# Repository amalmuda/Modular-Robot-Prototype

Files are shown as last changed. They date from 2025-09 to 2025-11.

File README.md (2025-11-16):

# The MATS - Modular Actuated Transforming System

MATS (Modular Actuated Transforming System) is a modular robot with two types of modules: Brick modules for connections and Joint modules with actuated servos. Unlike many modular robots, MATS allows easier morphology changes without manual disassembly and reassembly for each configuration.

The cable management of robotic systems like this can often also become messy, with wires running between modules. This project focused on creating a clean, efficient system with screw-free, robust connections to simplify assembly and maintain functionality. A unique feature of this robot is the absence of core modules; all Brick modules are identical, simplifying assembly and ensuring consistent functionality. I focused on a minimalist yet functional design to simplify manufacturing while ensuring intuitive use and visual appeal, covering both the fastening mechanism and cable management.

The modules are inspired by Revolve2, which is a framework focusing on modular robotics. The software used
to directly control the robot is the Dynamixel SDK, a software development kit that supports multiple programming tools and languages, including Python and ROS. For this project, I programmed the robot’s movements using Python and tested various custom movements that I developed. The robot communicates directly with a PC via a U2D2 USB communication converter.

This project developed a durable, visually appealing modular robot with easy-to-assemble modules, seamless connections, and efficient cable management. Its minimalist design simplifies use and supports future advancements in modular robotics.

## MATS Demo Video (dancing mode)

<p align="center">
  <a href="https://www.youtube.com/watch?v=7X1GoiLjF7E">
    MATS demo video (dancing mode)
  </a>
</p>

<p align="center">
  <b> Click the image to watch the MATS demo on YouTube (with sound)</b>
</p>

## Modular robot crawling

<p align="center">
  <a href="https://www.youtube.com/watch?v=GOCKxC3IZR8">
    Modular robot crawling
  </a>
</p>

<p align="center">
  <b>Click the image to watch on YouTube</b>
</p>

## Other configuration examples

<table>
  <tr>
    <td align="center">
      <a href="https://www.youtube.com/watch?v=6TiiAdvZFsY">
        Small worm configuration
      </a><br>
      <b>Small worm configuration</b><br>
      <sub></sub>
    </td>
    <td align="center">
      <a href="https://www.youtube.com/watch?v=PtgOzKhWjz0">
        Riverdancing quadruped
      </a><br>
      <b>Riverdancing quadruped</b><br>
      <sub></sub>
    </td>
  </tr>
  <tr>
    <td align="center">
      <a href="https://www.youtube.com/watch?v=ytFvpS4uCtc">
        4-legged breakdancing spider
      </a><br>
      <b>4-legged breakdancing spider</b><br>
      <sub></sub>
    </td>
    <td align="center">
      <a href="https://www.youtube.com/watch?v=Mg6dMusM-d4">
        Large snake configuration
      </a><br>
      <b>Large snake configuration</b><br>
      <sub></sub>
    </td>
  </tr>
</table>

# Tools and bill of materials

The following components were used in the development of MATS:

- U2D2 USB communication converter
- U2D2 Power Hub Board
- Dynamixel AX-18A servo
- 3D printed modules with PLA and ABS (CAD modelled in SolidWorks)
- Neodym magnets

**Complete list of bill of materials:**

Main components:
| Item | Description | Quantity 
| ---- | --- | ---
| 1 | Robotis U2D2 USB communication converter | 1 
| 2 | Robotis U2D2 Power Hub Board | 1 
| 3 | Dynamixel AX-18A servo | 8

Mounting components:
| Item | Description | Quantity 
| ---- | --- | ---
| 1 | Dynamixel-AX Bioloid FP04-F2 frame | 8 
| 2 | Dynamixel-AX Bioloid FP04-F3 frame | 8 
| 3 | RS PRO Neodym magnet 2.09 kg - 12 mm | 52

Connectors and wiring:
| Item | Description | Quantity 
| ---- | --- | ---
| 1 | Robotis 3P Extension PCB | 9 
| 2 | 3P Molex male to female adapter| 36 
| 3 | Self-assembled 3P Molex cable 4 cm | 36 
| 4 | Self-assembled 3P Molex cable 8 cm | 16 
| 5 | Self-assembled 3P Molex cable 18 cm | 16
| 6 | Self-assembled 3P Molex cable 50 - 100 cm | 1  
| 7 | Micro USB cable | 1  

Fasteners:
| Item | Description | Quantity 
| ---- | --- | ---
| 1 | Bioloid Plastic Busher BPF-BU| 8 
| 2 | Bioloid Plastic Washer BPF-WA| 8
| 3 | M3 bolts| 8
| 4 | M2 screws | 164
| 5 | M2 nuts | 32  

For 3D-printing:

| Part  | Material | Quantity | Infill | Layer height
| ----- | --- | --- | --- | ---
| Block module | ABS | 9  | 20 % | 0.2 mm 
| Servo holder | ABS | 16  | 20 % | 0.2 mm 
| Lid | PolyMaker PLA | 18  | 20 % | 0.2 mm 
| Power Hub Board base | PolyMaker PLA | 1  | 20 % | 0.2 mm 

## Firmware/software for the robot/prototype

Set up the environment:
```
$ conda create --name mats_env --file requirements.txt
$ conda activate mats_env
```
After installation, make sure:
- U2D2 Power Hub Board is turned ON and connected to the robot
- USB from the U2D2 is connected to your computer to the right port

Then you can run your Python files from the src folder with examples:
```
python breakdance.py
python wake_up.py
python dance.py
```
## Future work

### Design

- **Integrate Molex connectors:** Combine with mating connectors for seamless integration and use magnets for attachment and servo communication.
- **Expand connectivity:** Modify Brick modules for six-sided connectivity instead of four-sided to increase flexibility.
- **Add adapters:** Develop connectors for linking modules directly, including 360° revolute joints for modular manipulators.

### Hardware and software

- **Use a microcontroller or a Raspberry Pi:** Enable wireless control and communication with the robot.
- **Incorporate a battery as the power source:** Address the challenge of module size, or consider a core module to house the battery and hardware.
- **Use simulations, evolutionary algorithms, and artificial intelligence:** Optimize the robot’s movements efficiently.
- **Address the reality gap:** Develop methods to transfer optimized movements from simulations to the real-world robot, minimizing performance differences.

## Image gallery

<table>
  <!-- Row 1: evolution spans two columns -->
  <tr>
    <td align="center" colspan="2">
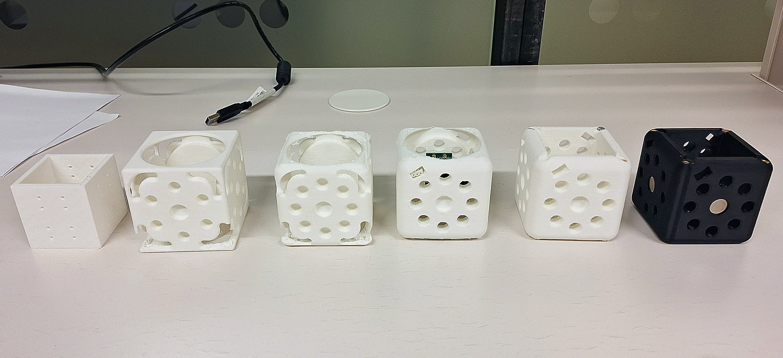
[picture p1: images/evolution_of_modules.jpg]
Evolution of the module design
      <br>
      <sub>Evolution of the module design</sub>
    </td>
  </tr>

  <!-- Row 2: assembled + exploded views -->
  <tr>
    <td align="center">
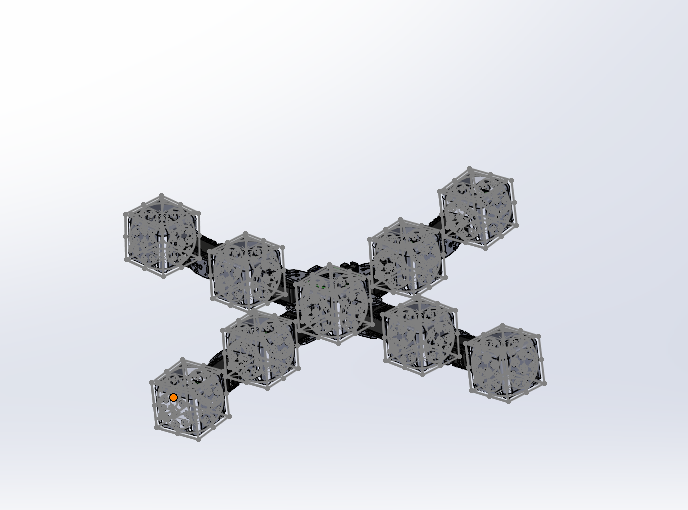
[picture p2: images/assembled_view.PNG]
Assembled module view in SolidWorks
      <br>
      <sub>Assembled module view in SolidWorks</sub>
    </td>
    <td align="center">
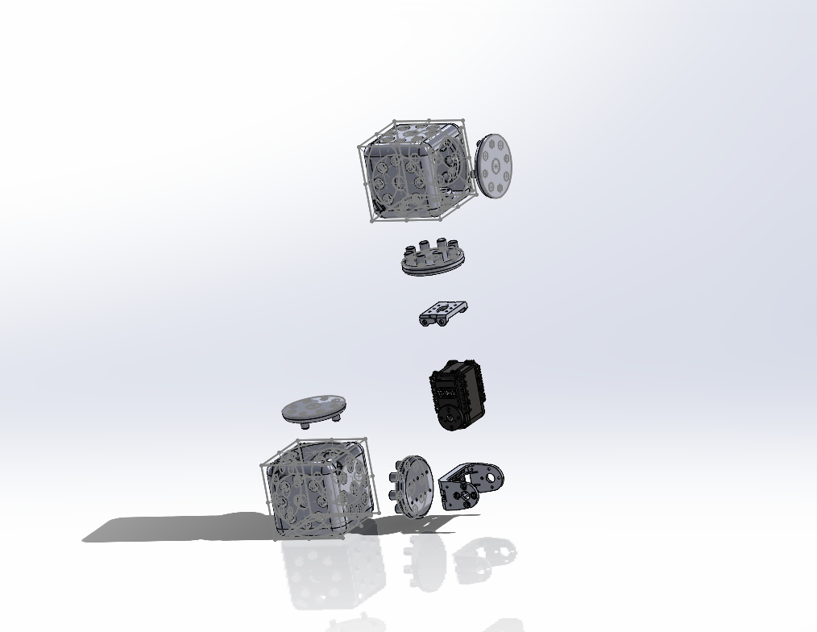
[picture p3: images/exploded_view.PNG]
Exploded module view in SolidWorks
      <br>
      <sub>Exploded module view in SolidWorks</sub>
    </td>
  </tr>

  <!-- Row 3: latest module + power hub -->
  <tr>
    <td align="center">
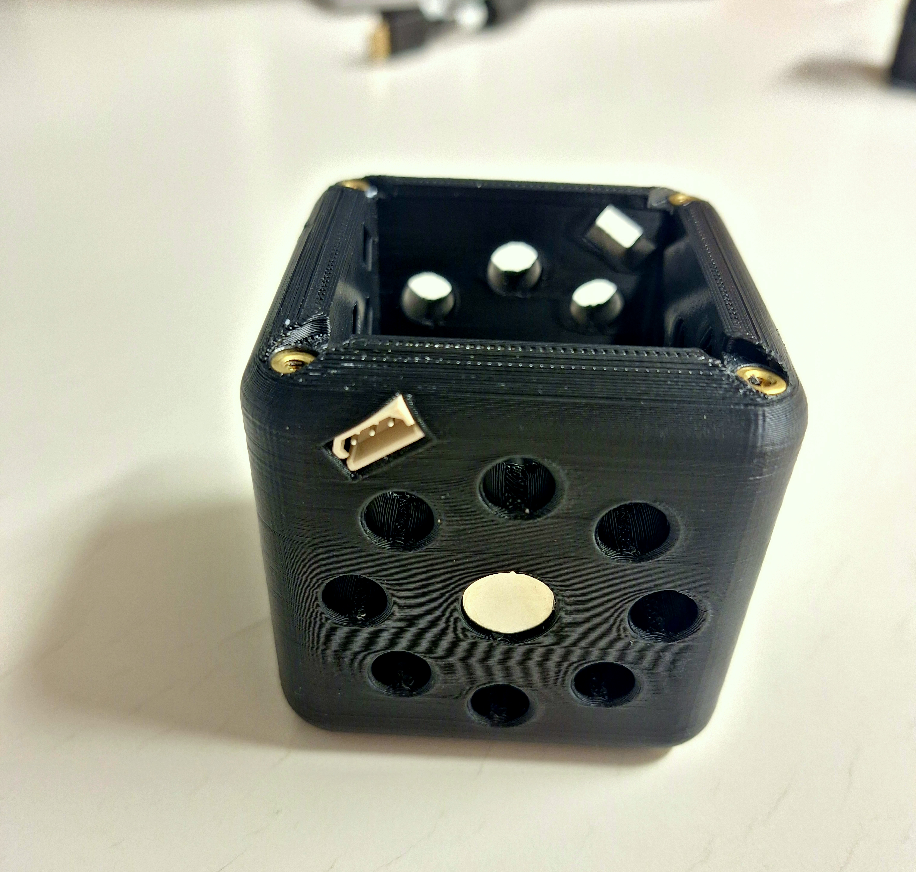
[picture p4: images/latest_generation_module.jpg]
Latest-generation module (ABS)
      <br>
      <sub>Latest-generation module (ABS)</sub>
    </td>
    <td align="center">
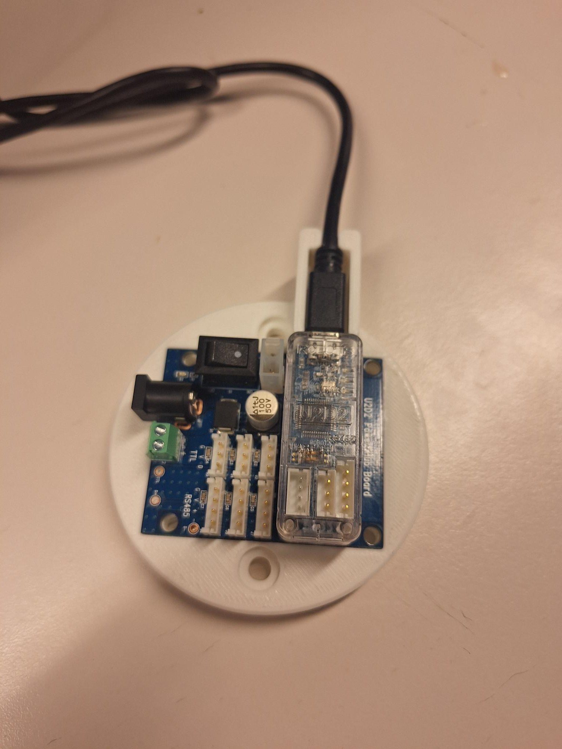
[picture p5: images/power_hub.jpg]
Power hub and control electronics
      <br>
      <sub>Power hub and control electronics</sub>
    </td>
  </tr>

  <!-- Row 4: spider simulation + robot in action -->
  <tr>
    <td align="center">
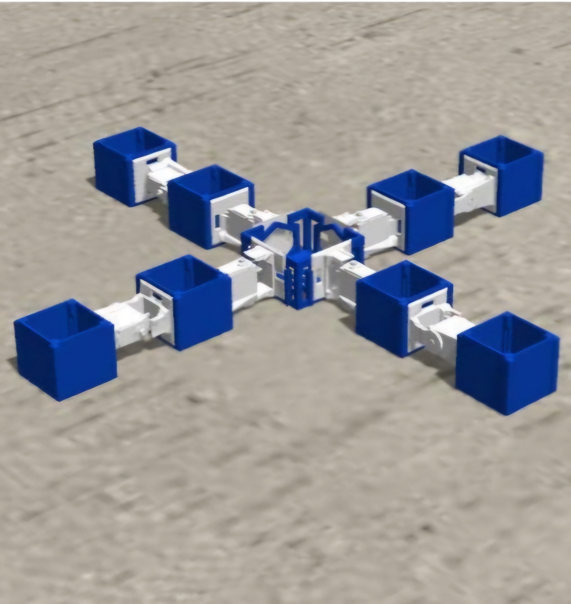
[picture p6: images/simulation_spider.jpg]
Spider-robot simulation in Revolve
      <br>
      <sub>Spider-robot simulation in Revolve</sub>
    </td>
    <td align="center">
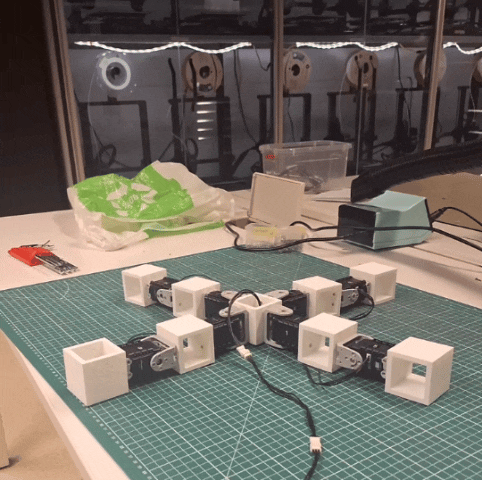
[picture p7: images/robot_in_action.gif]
Robot in action
      <br>
      <sub>Robot in action</sub>
    </td>
  </tr>
</table>

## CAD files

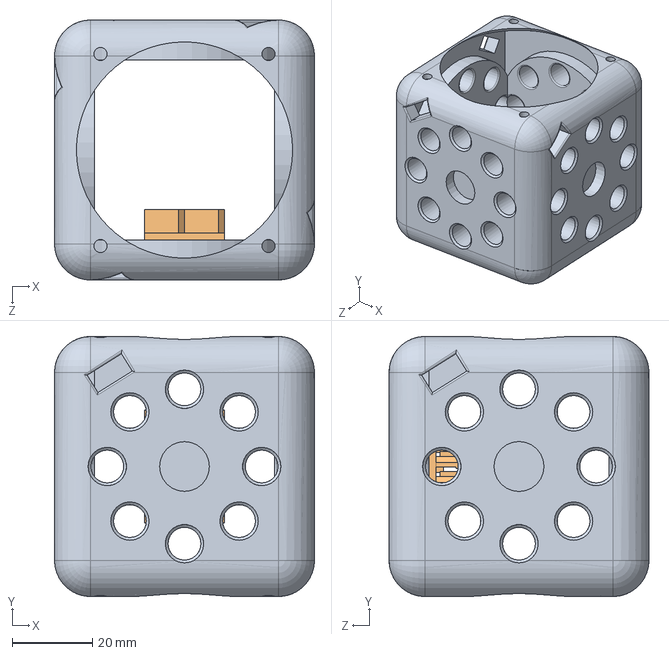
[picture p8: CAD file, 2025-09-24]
solidworks/brick_module_with_component.SLDASM
65.0 x 65.0 x 65.0 mm
brick_module
3P Extension PCB

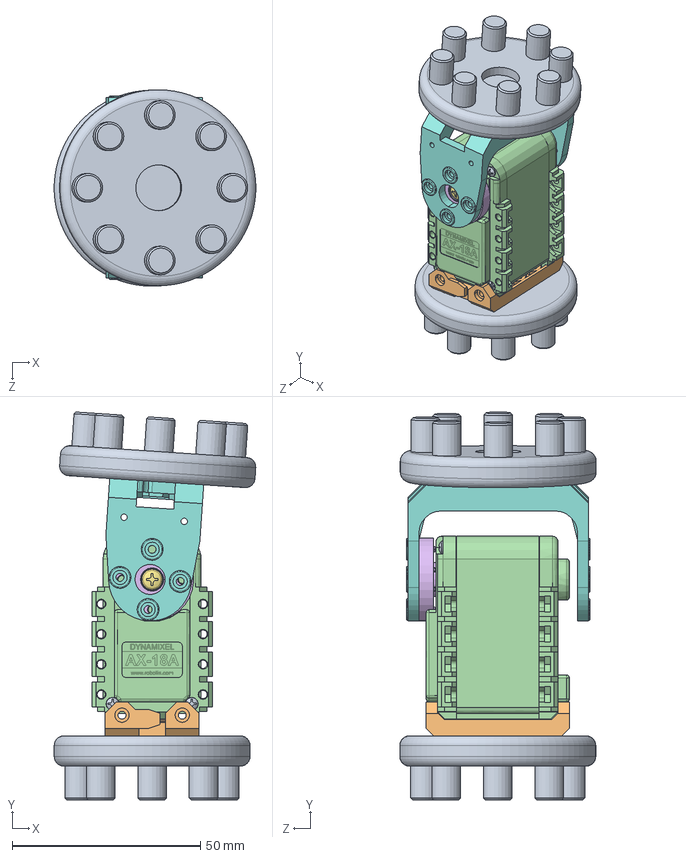
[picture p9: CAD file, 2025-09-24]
solidworks/servo_module.SLDASM
53.5 x 102.9 x 52.1 mm
Cover Screws^joint x 4
Insert M3^joint
3 Pins Connector^joint x 2
Body^joint
Wheel Gear^Horn Assembly_joint
Horn^Horn Assembly_joint
BHS M2x8^Horn Assembly_joint
FP04-F2.stp
servo_module x 2
FP04-F3.stp

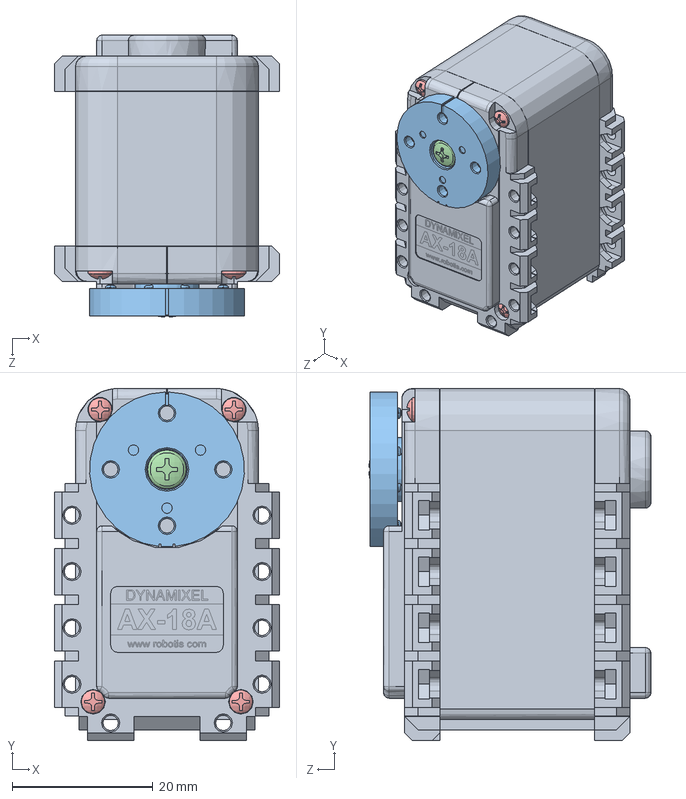
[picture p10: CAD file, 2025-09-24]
solidworks/Dynamixel AX-18A.SLDASM
32.0 x 50.0 x 40.1 mm
Body^AX-18A
Wheel Gear^Horn Assembly_AX-18A
Horn^Horn Assembly_AX-18A
BHS M2x8^Horn Assembly_AX-18A
Cover Screws^AX-18A x 4
3 Pins Connector^AX-18A x 2
Insert M3^AX-18A

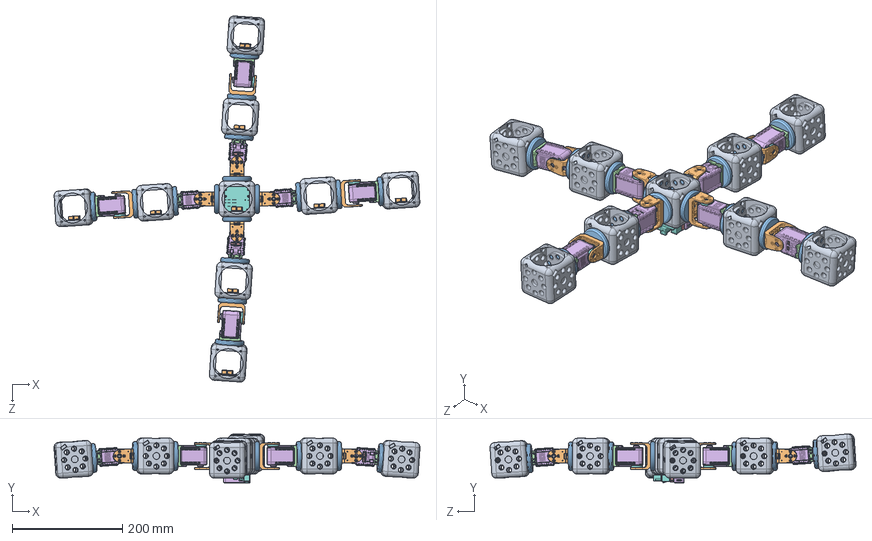
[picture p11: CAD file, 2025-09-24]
solidworks/assembled_spider_robot.SLDASM
663.6 x 88.8 x 663.5 mm
brick_module x 9
3P Extension PCB x 9
Cover Screws^joint x 32
Insert M3^joint x 8
3 Pins Connector^joint x 16
Body^joint x 8
Wheel Gear^Horn Assembly_joint x 8
Horn^Horn Assembly_joint x 8
BHS M2x8^Horn Assembly_joint x 8
FP04-F2.stp x 8
servo_module x 16
FP04-F3.stp x 8
39281023.prt.stp
JST-B4B-EH-A.PRT.1.stp x 3
JST-B3B-EH-A.PRT.1.stp x 3
Board.stp
JST-B3B-EH-A.PRT.stp
JST-B4B-EH-A.PRT.stp
JST-B4B-PH-K-S.PRT.stp
MICRO_USB_2_0_CONNECTOR__AB_REC.PRT.stp
PCB_U2D2.PRT.stp
U2D2_CASING.PRT.stp

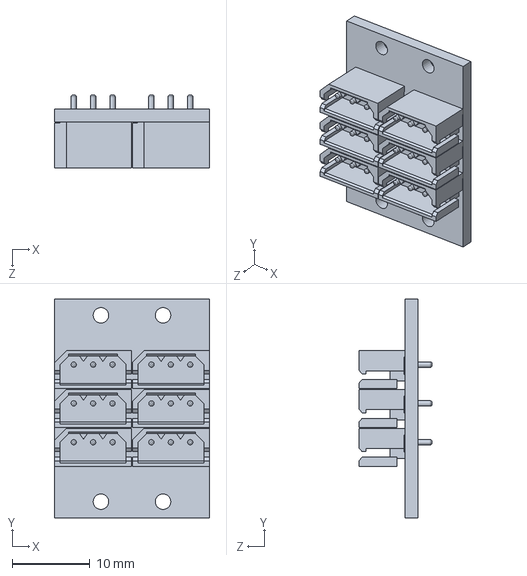
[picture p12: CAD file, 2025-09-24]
solidworks/3P Extension PCB.SLDPRT
20.0 x 28.2 x 9.40 mm

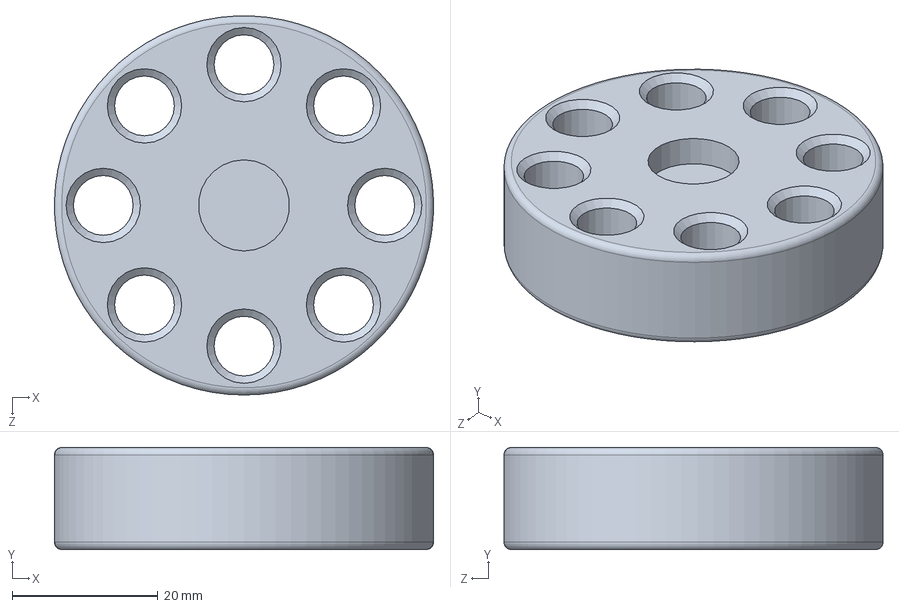
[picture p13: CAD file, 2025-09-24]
solidworks/servo_adapter.SLDPRT
52.0 x 14.0 x 52.0 mm

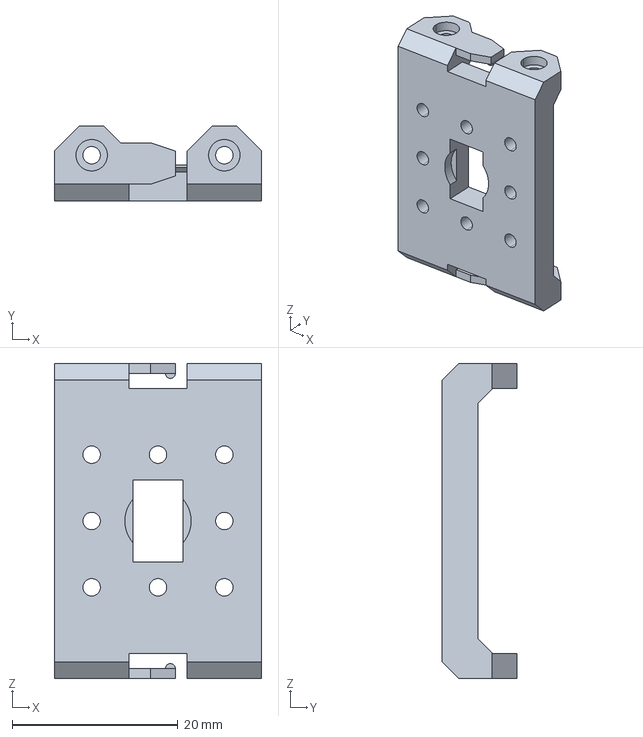
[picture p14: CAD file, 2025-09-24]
solidworks/FP04-F3.stp
25.0 x 9.00 x 38.0 mm

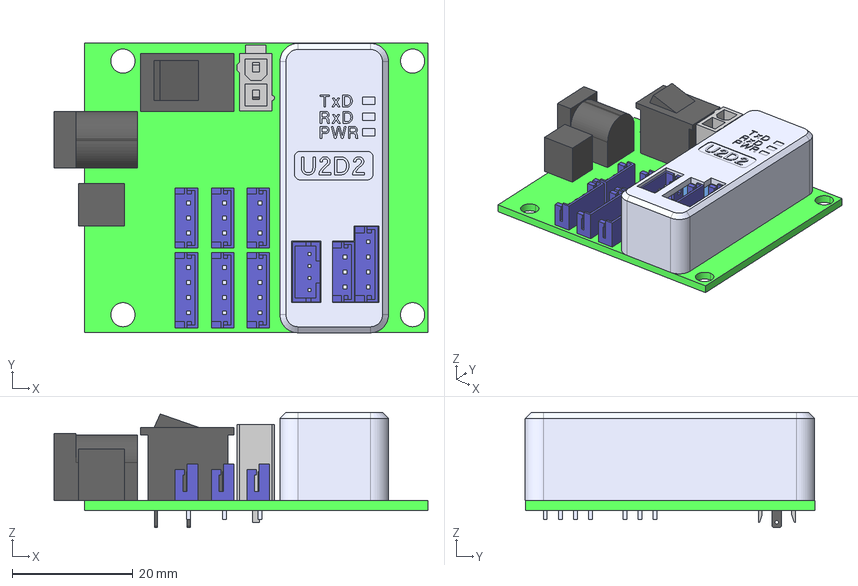
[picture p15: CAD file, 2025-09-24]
solidworks/U2D2 Power Hub Board.stp
62.0 x 48.0 x 19.1 mm
JST-B4B-EH-A.PRT.1 x 3
JST-B3B-EH-A.PRT.1 x 3
Board
39281023.prt
JST-B3B-EH-A.PRT
JST-B4B-EH-A.PRT
JST-B4B-PH-K-S.PRT
MICRO_USB_2_0_CONNECTOR__AB_REC.PRT
PCB_U2D2.PRT
U2D2_CASING.PRT

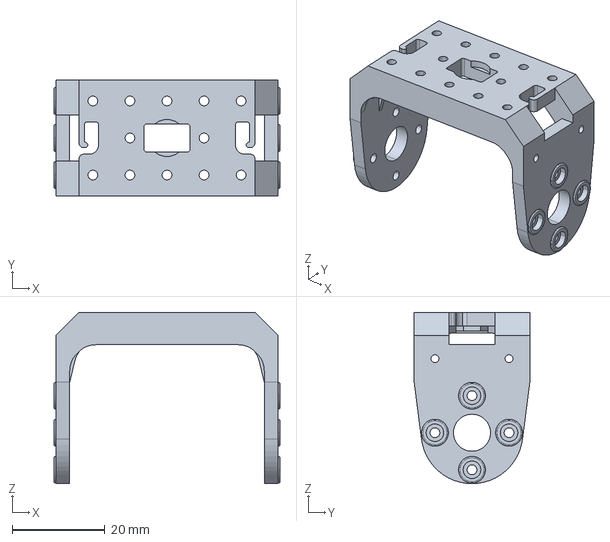
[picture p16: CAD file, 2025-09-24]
solidworks/FP04-F2.stp
48.8 x 25.0 x 37.0 mm

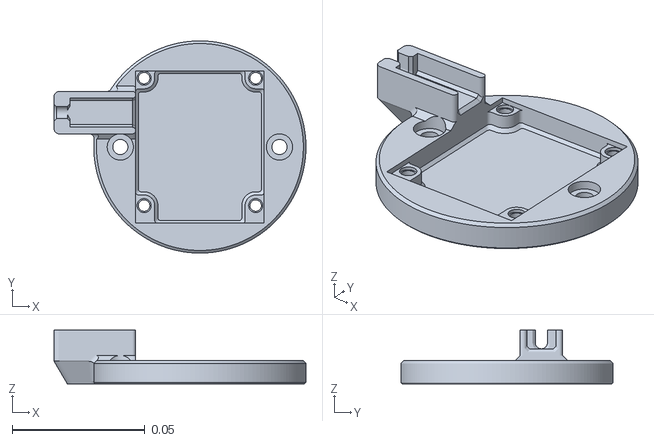
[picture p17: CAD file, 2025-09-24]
solidworks/PHB base.stl
0.095 x 0.08 x 0.0202

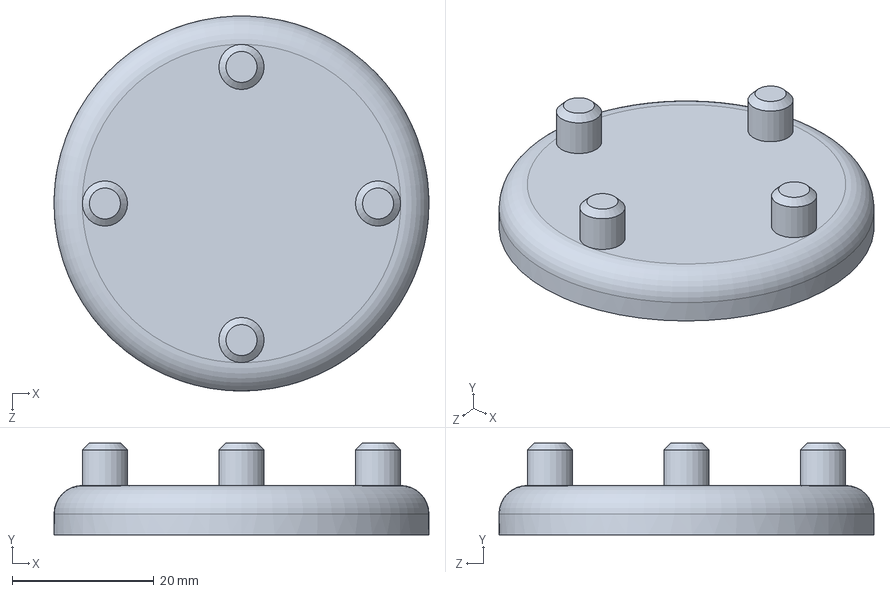
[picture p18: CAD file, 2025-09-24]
solidworks/lid.SLDPRT
53.0 x 13.0 x 53.0 mm

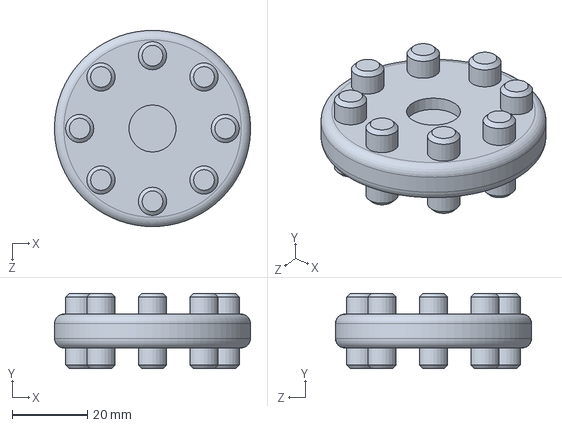
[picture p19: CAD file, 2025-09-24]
solidworks/block_adapter.SLDPRT
52.0 x 20.0 x 52.0 mm

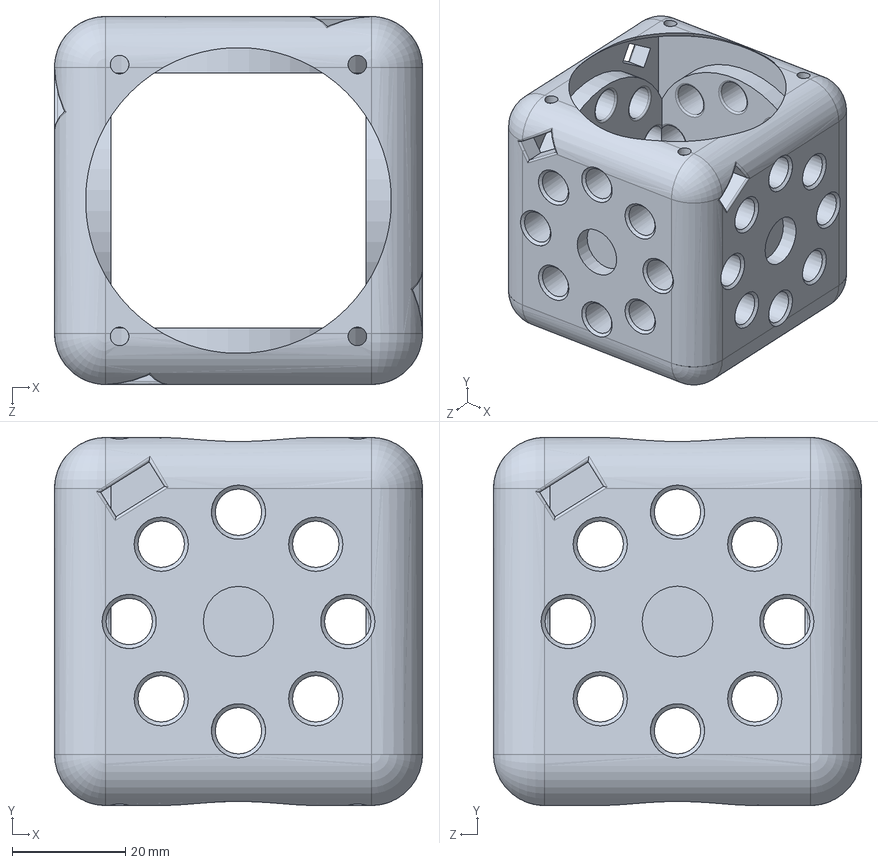
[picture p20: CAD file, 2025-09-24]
solidworks/brick_module.SLDPRT
65.0 x 65.0 x 65.0 mm

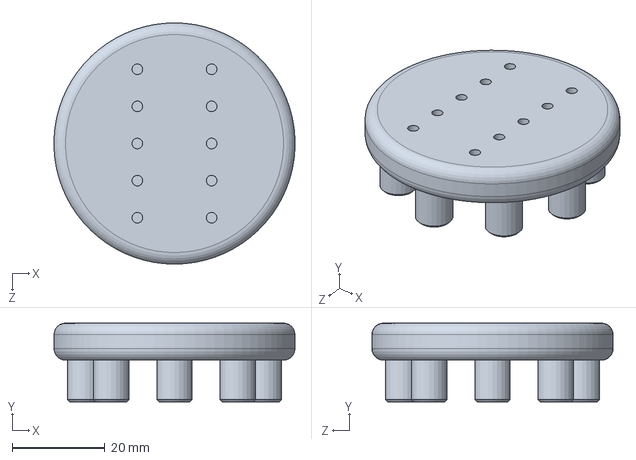
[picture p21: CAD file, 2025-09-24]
solidworks/servo_holder.SLDPRT
52.0 x 17.0 x 52.0 mm

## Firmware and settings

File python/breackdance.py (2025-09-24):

import time
from dynamixel_sdk import *  # Dynamixel SDK library

# Control table addresses
ADDR_PRO_GOAL_POSITION = 30
ADDR_PRO_TORQUE_ENABLE = 24

# Protocol version
PROTOCOL_VERSION = 1.0

# Default settings
DXL_ID = [1, 2, 3, 4, 5, 6, 7, 8]  # Servo IDs 1 to 8
BAUDRATE = 1000000
DEVICENAME = 'COM3'
TORQUE_ENABLE = 1
GOAL_POSITION_ZERO = 512  # 512 corresponds to 0 degrees in Dynamixel

# Final standing positions for each servo
STANDING_POSITIONS = {
    1: 350,  # Hip angle for Leg 1
    5: 650,  # Knee angle for Leg 1
    2: 670,  # Hip angle for Leg 2
    6: 370,  # Knee angle for Leg 2
    3: 350,  # Hip angle for Leg 3
    7: 650,  # Knee angle for Leg 3
    4: 670,  # Hip angle for Leg 4
    8: 370,  # Knee angle for Leg 4
}

# Initialize PortHandler and PacketHandler
portHandler = PortHandler(DEVICENAME)
packetHandler = PacketHandler(PROTOCOL_VERSION)

# Open port
if not portHandler.openPort():
    print("Failed to open the port")
    exit()

# Set port baudrate
if not portHandler.setBaudRate(BAUDRATE):
    print("Failed to set the baudrate")
    exit()

# Enable torque for each servo
for dxl_id in DXL_ID:
    packetHandler.write1ByteTxRx(portHandler, dxl_id, ADDR_PRO_TORQUE_ENABLE, TORQUE_ENABLE)

# Step 1: Gradually stand up by incrementally moving to each standing position
def gradual_stand_up():
    increments = 10  # Number of steps to reach the final position
    for step in range(1, increments + 1):
        for dxl_id, final_position in STANDING_POSITIONS.items():
            # Calculate intermediate position
            initial_position = GOAL_POSITION_ZERO  # Starting position (0 degrees)
            intermediate_position = initial_position + (final_position - initial_position) * step // increments
            # Set the servo to the intermediate position
            packetHandler.write2ByteTxRx(portHandler, dxl_id, ADDR_PRO_GOAL_POSITION, intermediate_position)
        
        # Short delay for servos to move in each step
        time.sleep(0.2)

# Execute the gradual stand-up sequence
gradual_stand_up()

# Wait for a moment in the standing position
time.sleep(1)

# Step 2: Set all servos back to 0 degrees (flat position)
for dxl_id in DXL_ID:
    packetHandler.write2ByteTxRx(portHandler, dxl_id, ADDR_PRO_GOAL_POSITION, GOAL_POSITION_ZERO)

# Wait for servos to reach 0 degrees
time.sleep(2)

# Close port
portHandler.closePort()

import time
from dynamixel_sdk import *  # Dynamixel SDK library

# Control table addresses
ADDR_PRO_GOAL_POSITION = 30
ADDR_PRO_TORQUE_ENABLE = 24

# Protocol version
PROTOCOL_VERSION = 1.0

# Default settings
DXL_ID = [1, 2, 3, 4, 5, 6, 7, 8]  # Servo IDs 1 to 8
BAUDRATE = 1000000
DEVICENAME = 'COM3'
TORQUE_ENABLE = 1

# Standing position angles for each servo
# These values are estimated for a basic standing position
STANDING_POSITIONS = {
    1: 350,  # Hip angle for Leg 1 (servo 1)
    5: 650,  # Knee angle for Leg 1 (servo 5)
    2: 670,  # Hip angle for Leg 2 (servo 2)
    6: 370,  # Knee angle for Leg 2 (servo 6)
    3: 350,  # Hip angle for Leg 3 (servo 3)
    7: 650,  # Knee angle for Leg 3 (servo 7)
    4: 670,  # Hip angle for Leg 4 (servo 4)
    8: 370,  # Knee angle for Leg 4 (servo 8)
}

# Initialize PortHandler and PacketHandler
portHandler = PortHandler(DEVICENAME)
packetHandler = PacketHandler(PROTOCOL_VERSION)

# Open port
if not portHandler.openPort():
    print("Failed to open the port")
    exit()

# Set port baudrate
if not portHandler.setBaudRate(BAUDRATE):
    print("Failed to set the baudrate")
    exit()

# Enable torque for each servo
for dxl_id in DXL_ID:
    packetHandler.write1ByteTxRx(portHandler, dxl_id, ADDR_PRO_TORQUE_ENABLE, TORQUE_ENABLE)

# Stand up function
def stand_up():
    # Set each servo to its respective standing position
    for dxl_id, goal_position in STANDING_POSITIONS.items():
        packetHandler.write2ByteTxRx(portHandler, dxl_id, ADDR_PRO_GOAL_POSITION, goal_position)

    # Wait for servos to reach position
    time.sleep(2)

# Execute the stand-up sequence
stand_up()

# Close port
portHandler.closePort()

import time
from dynamixel_sdk import *  # Dynamixel SDK library

# Control table addresses
ADDR_PRO_GOAL_POSITION = 30
ADDR_PRO_TORQUE_ENABLE = 24

# Protocol version
PROTOCOL_VERSION = 1.0

# Default settings
DXL_ID = [1, 2, 3, 4, 5, 6, 7, 8]  # Servo IDs 1 to 8
BAUDRATE = 1000000
DEVICENAME = 'COM3'
TORQUE_ENABLE = 1
GOAL_POSITION_ZERO = 512  # 512 corresponds to 0 degrees in Dynamixel

# Initialize PortHandler and PacketHandler
portHandler = PortHandler(DEVICENAME)
packetHandler = PacketHandler(PROTOCOL_VERSION)

# Open port
if not portHandler.openPort():
    print("Failed to open the port")
    exit()

# Set port baudrate
if not portHandler.setBaudRate(BAUDRATE):
    print("Failed to set the baudrate")
    exit()

# Enable torque for each servo
for dxl_id in DXL_ID:
    packetHandler.write1ByteTxRx(portHandler, dxl_id, ADDR_PRO_TORQUE_ENABLE, TORQUE_ENABLE)

# Set all servos to 0 degrees
for dxl_id in DXL_ID:
    packetHandler.write2ByteTxRx(portHandler, dxl_id, ADDR_PRO_GOAL_POSITION, GOAL_POSITION_ZERO)

# Wait for servos to reach position
time.sleep(2)

# Close port
portHandler.closePort()

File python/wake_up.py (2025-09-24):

import time
from dynamixel_sdk import *  # Dynamixel SDK library

# Control table addresses
ADDR_TORQUE_ENABLE = 24
ADDR_GOAL_POSITION = 30
ADDR_PRESENT_POSITION = 36
ADDR_MOVING_SPEED = 32

# Servo configuration
PROTOCOL_VERSION = 1.0
BAUDRATE = 1000000
DEVICENAME = 'COM3'  # Adjust to your setup

# Servo IDs
TRIPOD_1 = [1, 4, 7]  # Tripod 1: 1 (front-left), 4 (back), 7 (front-right)
TRIPOD_2 = [2, 5, 8]  # Tripod 2: 2 (front-right), 5 (back), 8 (front-left)

# Conversion function for angle to Dynamixel position
def angle_to_position(angle):
    return int((angle + 150) / 300 * 1023)

# Initialize PortHandler and PacketHandler
port_handler = PortHandler(DEVICENAME)
packet_handler = PacketHandler(PROTOCOL_VERSION)

if not port_handler.openPort():
    print("Failed to open port!")
    exit()
if not port_handler.setBaudRate(BAUDRATE):
    print("Failed to set baudrate!")
    exit()

# Function to move servos
def move_servos(ids, positions, delay=0.5):
    for i, servo_id in enumerate(ids):
        position = positions[i]
        packet_handler.write2ByteTxRx(port_handler, servo_id, ADDR_GOAL_POSITION, position)
    time.sleep(delay)

# Enable torque
for servo_id in range(1, 9):
    packet_handler.write1ByteTxRx(port_handler, servo_id, ADDR_TORQUE_ENABLE, 1)

try:
    # 1. Starting Standing Position (ensure hips at 0°, knees at -90°)
    stand_hip_positions = angle_to_position(0)
    stand_knee_positions = angle_to_position(-90)
    move_servos(range(1, 9), [stand_hip_positions] * 4 + [stand_knee_positions] * 4)

    # 2. Lift Tripod 1 (1, 4, 7)
    lift_knee_positions = angle_to_position(-60)
    move_servos(TRIPOD_1, [lift_knee_positions] * 3)

    # 3. Swing Tripod 1 Forward
    move_servos([1, 7], [angle_to_position(30), angle_to_position(30)])  # Hips swing forward
    move_servos([4], [angle_to_position(-30)])  # Back leg swings forward

    # 4. Place Tripod 1 Down
    move_servos(TRIPOD_1, [stand_knee_positions] * 3)

    # 5. Lift Tripod 2 (2, 5, 8)
    move_servos(TRIPOD_2, [lift_knee_positions] * 3)

    # 6. Swing Tripod 2 Forward
    move_servos([2, 8], [angle_to_position(30), angle_to_position(30)])  # Hips swing forward
    move_servos([5], [angle_to_position(-30)])  # Back leg swings forward

    # 7. Place Tripod 2 Down
    move_servos(TRIPOD_2, [stand_knee_positions] * 3)

finally:
    # Disable torque
    for servo_id in range(1, 9):
        packet_handler.write1ByteTxRx(port_handler, servo_id, ADDR_TORQUE_ENABLE, 0)
    port_handler.closePort()

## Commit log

2024-11-06 assignment5 files
    [3P Extension PCB.SLDPRT, Dynamixel AX-18A.SLDASM, FP04-F2.stp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]
2025-11-15 Restructure folders and remove files
    [3P Extension PCB.SLDPRT, Dynamixel AX-18A.SLDASM, FP04-F2.stp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]
